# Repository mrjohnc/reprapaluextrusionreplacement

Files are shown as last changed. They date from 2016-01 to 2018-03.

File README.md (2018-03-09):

# reprapaluextrusionreplacement
Designs for a 3D printed replacement of Aluminium extrusion frames on Reprap 3d printers. 

Here are the main advantages and disadvantages that I can see of having a 3d printed frame:

Advantages:

    Make the printer more self replicating (I think if it was possible it would be one of the highest percentage self replicating printers)
    Reduce the number materials needed to create a kit for people having trouble sourcing the parts like me
    Potentially reduce cost (although maybe not by a lot)
    Make it easier for people to experiment with different designs for the frame
    You can have it in what ever colour you want

Disadvantages:

    Much longer print time
    Potentially weaker frame

What I'm showing is where I have got to when I ran out of time, I would really love it if others could pick up where I've left off. I wont have access to my printer for the next few months but very happy to help in other ways.

The current design was done in Tinkercad and is quite simple, there are three different parts:

    Internal rods of 100mm in length

external sheathes (100m length) which come in two versions which can be shortened to create different length frame sides.

    end pieces which will screw into the existing corner pieces
    middle sheathes which are just a long tube. 

There were several previous iterations that were simply too complicated, I think my current approach has a few strengths:

    The end results seem very straight
    Uses PLA which means you don't need a heated bed
    The parts are easy to print and can be printed at a higher temperature to ensure good layer bonding
    The parts are printed with the rods lying down and the sheathes on their ends so printed layers run in different directions meaning the parts are strong in all directions.
    Simple construction, you only need a wooden mallet or some other tool to encourage the parts together
    Strong joins between parts, the inner rods join in the middle of the outer sheathes
    The longest dimension of parts is 100mm meaning it can be printed on a small print volume printer.

Printing notes:
I printed everything seen with Hatchbox PLA using a Printrbot Simple Metal with a E3D V6 head with 0.3mm nozzle. I used a 0.6 outer shell, 35% infill, 2mm layer heights and printed at 217 degrees C with a cooling fan.

The internal rods are printed at around 95% size so they fit snuggly inside the outer sheathes. I printed shorter test pieces to find the right scale however shorter pieces have slightly less friction when pushing them together, I found 96% worked fine with the test pieces but 95% worked much better with the full size pieces. It also helps a lot in getting the parts to fit well to scrape the corners of the internal rods a bit with a sharp knife.

Issues

    The time it takes to print the pieces is quite long
    Tolerance for print size of internal rods is very small, however its easy to make shorter lengths to check tolerances
    The direction for the join for the internal rods is the sample as the direction for the direction of the print layers in the outer sheath meaning this could be a weak point but I think this could be fixed with glue.
    You have to scrape the edges off the internal rods so that the size is correct for the sides of it to grip the sides of the outer sheath.
    Once the parts are put together its not possible to take them apart again
    Whilst this maintains the width of the Aluminum you're not able to screw the other printed parts into the rods so would have to adapt the or make much wider rods to accommodate screw holes, here is a test piece.
    Image error
    Running getimagesize() on the image data failed
    open image URL

Ideas for future versions

    use a glue to join parts together, perhaps using a very rigid glue e.g superglue or araldite to increase rigidity of the frame. This could help with both the potential weak point in the middle of each section and make it easier to push the parts together because it would reduce friction when inserting the rods
    Round the edges of the internal rods
    Create some sort of mark on the internal rods so it is clear where the middle of the internal rods are
    Use transparent material to see when the parts are fitting together correctly

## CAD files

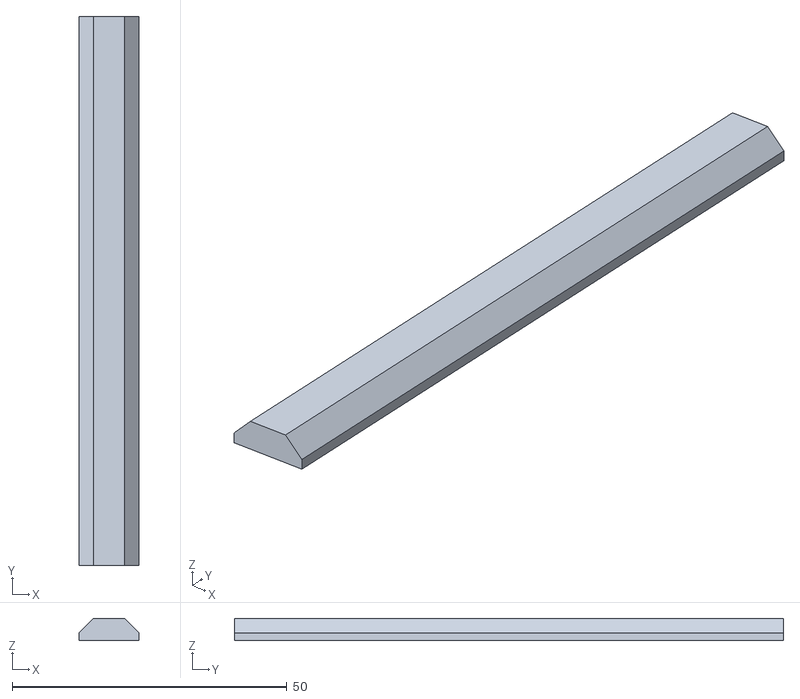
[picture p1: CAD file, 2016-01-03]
100mm vslot connector.stl
11.0 x 100.0 x 4.10

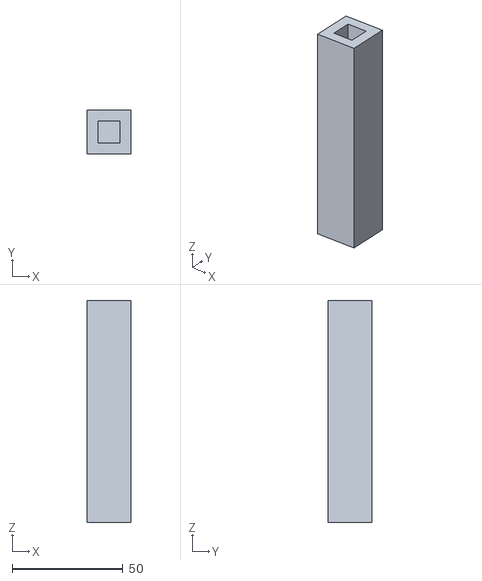
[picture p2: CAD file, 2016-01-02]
rods and sheath approach/end sheath.stl
20.0 x 20.0 x 100.0

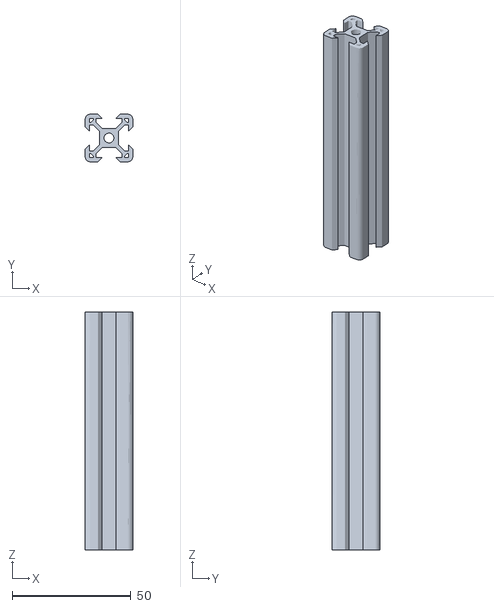
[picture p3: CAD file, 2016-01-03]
20x20mm vslot profile.stl
20.0 x 20.0 x 100.0

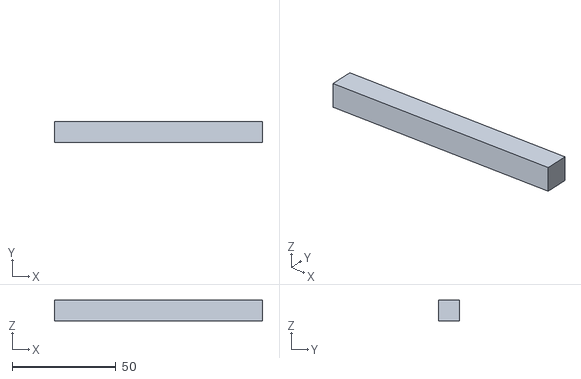
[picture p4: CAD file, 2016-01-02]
rods and sheath approach/internal rod.stl
100.0 x 10.0 x 10.0

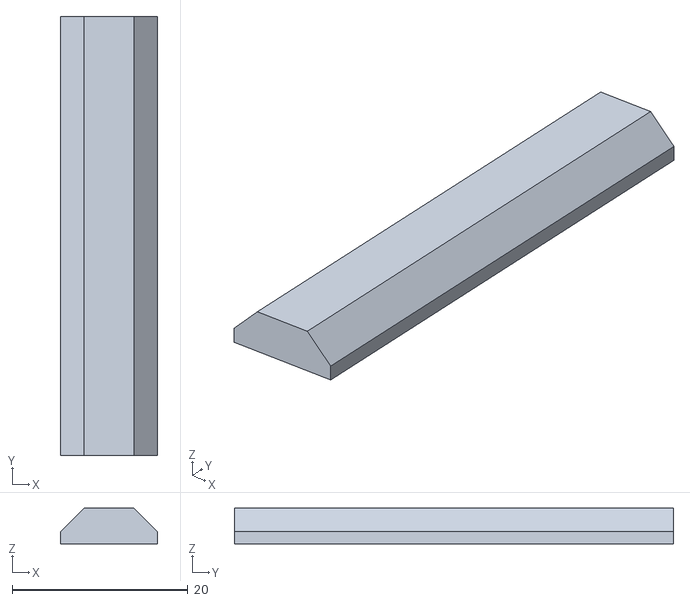
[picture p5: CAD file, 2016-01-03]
50 mm vslot connector.stl
11.0 x 50.0 x 4.10

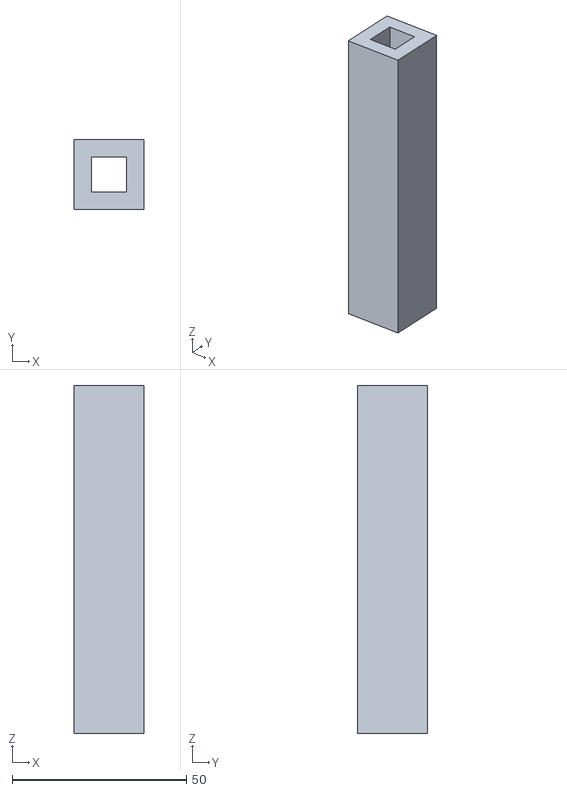
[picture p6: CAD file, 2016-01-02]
rods and sheath approach/middle sheath.stl
20.0 x 20.0 x 100.0
